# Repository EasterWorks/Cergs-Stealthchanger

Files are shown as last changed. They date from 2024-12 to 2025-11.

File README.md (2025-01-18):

# Cergs-Stealthchanger

Repo status: READY (ready for public reference)  

This repo contains my configurations and customizations for my Stealthchanger build.  

This repo may be useful to you if you have similar design constraints and requirements to my own:

- You have a 300mm Voron 2.4r2.
- Your mainboard is a BTT Octopus Pro or board with similar capabilities.
- You want to use Stealthburner toolheads with the E3D Revo hotend ecosystem.
- You are using LDO's Nitehawk-SB or Nitehawk-36 toolhead boards and Isik Tech's Birds' Nest for toolhead board networking.
- You are using the standard X/Y endstops that are located on the intersection of the X and Y axiis rather than the toolhead-mounted endstops or sensorless homing.
- You are want to use OptoTAP v2.4.1 for your Z axis probe and endstop trigger.
- You are me in the future and nuked your config files again or forgot how to calibrate something.

In addition, I have edited and provided a few STL's that improve upon the original design and/or make it more suitable for the above considerations.  

This repo is under construction. The top line of this readme document says "Repo status" - I will keep this up to date as I update my progress on the toolchanger project.

If you have any questions about necessary plugins or part designs, please reach out to the original creators (whom will be listed and credited when their content is used). I also HIGHLY recommend joining the public Stealthchanger Discord channel, link here: https://discord.gg/kXuEYBsa

## Mile-High Overview of the Stealthchanger

[This](https://github.com/EasterWorks/Cergs-Stealthchanger/blob/main/mile-high-overview-of-the-stealthchanger.md) is a shorter document than the Hardware and Calibration document which is going to cover the basic concepts as a toe-dip. 

## How to Stealthchanger

I have created a guide in this repo that covers all the steps I took from day 1 to fully-functional. You can find it here: https://github.com/EasterWorks/Cergs-Stealthchanger/blob/main/Hardware-And-Calibration.md

## Extrapolation

You will notice that there is a folder named "Extrapolation". This includes experiments I've done with the Stealthchanger ecosystem to try to make it more approachable, more reliable, and overall improved. It primarily has a focus on lessons learned for now, but I will include files and information for anything that I tried that I found particularly valuable as well.

## Credits:  
Viesturz, "tapchanger"  
- https://github.com/viesturz/tapchanger  

DraftShift Design, "StealthChanger"  
- https://github.com/DraftShift/StealthChanger  

DraftShift Design & Viesturz "klipper-toolchanger"  
- https://github.com/viesturz/klipper-toolchanger (use this one until DraftShift greenlights their version for public use!)
- https://github.com/DraftShift/klipper-toolchanger  

Thiessen with DraftShift Design for being INCREDIBLY helpful and patient with helping the community find answers when needed.

The Stealthchanger community for being encouraging and offering guidance.

All the people I've linked under printed part recommendations in the above guide.

## Updates:

12/13/2024:  
- Added my initial configs assortment. Some are incomplete.  

12/24/2024:
- Added OrcaSlicer start gcode.

12/29/2024:
- Updated all CFG files as the project is now functional (in testing)

12/30/2024:
- Final touches on cfg examples.
- Refined and added a ton of info to the guide document.
- Updated repo status from "IN TESTING" to "READY".

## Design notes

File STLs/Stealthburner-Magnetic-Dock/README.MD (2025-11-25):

Current options allow for both Revo and Repido 2 hotends (credit to nicksnoopy on Discord for the Rapido 2 files). Uses 8x 6x3mm Neodymium magnets (recommend N52). Adhere to shaped cutouts using heat-tolerant superglue or epoxy (I find that Loctite Professional Liquid is sufficient for 50-60c chamber temps).

- dock-base.stl:
Replaces the base piece from the Modular Docks repo. Needs 4x magnets.

- [hotend]-front.stl:
SB front hotend assembly for chosen hotend. Needs 2x magnets.

- [hotend]-rear.stl:
SB rear hotend assembly for chosen hotend. Needs 2x magnets.

Rapido V2 files provided by nicksnoopy on Discord.

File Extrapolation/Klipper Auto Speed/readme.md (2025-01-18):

Once your Stealthchanger is functioning reliably, I have found it valuable to run Kilpper Auto Speed by Anonoei, which you can find here:

https://github.com/Anonoei/klipper_auto_speed

For improving clarity, here is the entire process:

### Ensure Klippy-env is up to date:

```
sudo apt install python3
sudo apt install python3-numpy
sudo systemctl stop klipper
python3 -m venv --update ~/klippy-env
~/klippy-env/bin/pip install -r "~/klipper/scripts/klippy-requirements.txt"
```

### Install Klipper Auto Speed:

```
cd ~
git clone https://github.com/Anonoei/klipper_auto_speed.git
cd klipper_auto_speed
./install.sh
```

Note: Make sure you copy and paste the second line including the repo link into your SSH terminal. I initially typed it by hand and it prompted me to enter Github user credentials. If you copy and paste it, however, it doesn't do that. (shrug)

### Update Printer.cfg:

Copy and paste this to the bottom of your printer.cfg file (don't uncomment the commented-out lines):

```
[auto_speed]
#axis: diag_x, diag_y  ; One or multiple of `x`, `y`, `diag_x`, `diag_y`, `z`

#margin: 20            ; How far away from your axes to perform movements

#settling_home: 1      ; Perform settling home before starting Auto Speed
#max_missed: 1.0       ; Maximum full steps that can be missed
#endstop_samples: 3    ; How many endstop samples to take for endstop variance

#accel_min: 1000.0     ; Minimum acceleration test may try
#accel_max: 50000.0    ; Maximum acceleration test may try
#accel_accu: 0.05      ; Keep binary searching until the result is within this percentage

#velocity_min: 50.0    ; Minimum velocity test may try
#velocity_max: 5000.0  ; Maximum velocity test may try
#velocity_accu: 0.05   ; Keep binary searching until the result is within this percentage

#derate: 0.8           ; Derate discovered results by this amount

#validate_margin: Unset      ; Margin for VALIDATE, Defaults to margin
#validate_inner_margin: 20.0 ; Margin for VALIDATE inner pattern
#validate_iterations: 50     ; Perform VALIDATE pattern this many times

#results_dir: ~/printer_data/config ; Destination directory for graphs
```

Note: Technically you only need to include "[auto_speed]", but I advise grabbing the params as well so you can adjust if needed.

### Running Auto Speed:

Klipper Auto Speed has several macros you can utilize, though the fast way to do this is to just use AUTO_SPEED. You can append AXIS=[axis] to specify the axis you want to test. Example:

You want to test the Z axis.
```
AUTO_SPEED AXIS=Z
```

If you DON'T specify an axis, the X and Y axes will be tested.

Of incredible importance: Ensure your X/Y/Z max positions are accurate. My Voron 2.4 on paper has a 300mm max Z position, but in practice, it actually runs into hardware limitations at 280mm. I had never edited this parameter to be accurate to reality, so it was still set to 300mm, and my gantry tried to go to heaven when I first tried to test the Z axis. 

### What it does and how it works:

AUTO_SPEED will take around 5-10 minutes to run for each axis. It will home many times during this process.

For its testing procedure, Auto Speed will home the gantry to measure zero position, then do a short, quick move on the axis/axes being tested. Once done with the quick move, it will re-home and compare the home position to where the tool believed it was after the quick move. This determines step loss.

As the procedure continues, the short, quick moves will become more and more aggressive until Klipper Auto Speed sees a more than acceptable number of steps are being lost. It will then present max speeds and accelerations in the following format over the console:

```
AUTO SPEED found recommended acceleration and velocity after 243.31s
| DIAG X max: a23487 v421
| DIAG Y max: a23487 v421
Recommended accel: 23487
Recommended velocity: 421
```

### What to do with the results:

The results that Klipper Auto Speed will present are essentially the maximum acceptable **travel moves** for your printer. You don't want to run the printer at its absolute max all the time, so take about 20% off the top and use those as your new speed and acceleration maxes for the relevant axes.

After doing this and restarting firmware, I advise running a QGL with your finger on the E-stop. QGL will use the max X/Y/Z speeds and accelerations for travel moves. If you hear groaning, belt skipping, or anything else concerning, dial back the speed by another 10%. Repeat until expensive sounds stop happening, then slowly increase it until they start again. Then decrease slightly below that level, and you have your max X/Y/Z travel movements.

### Use case:

The default speeds and accelerations for the Z axis in the Voron 2.4 printer.cfg are :

```
max_z_velocity: 15 			#Max 15 for 12V TMC Drivers, can increase for 24V
max_z_accel: 350
```

In my experience, even doubling that default speed to 30 since Vorons run on 24v, this results in a 24-second toolchange procedure. It could be worse, but it could also be a whole lot better.

After running Klipper Auto Speed, I found the physical limitations of the Z axis were actually quite a lot higher:

```
AUTO SPEED found recommended acceleration and velocity after 619.64s
| Z max: a65974 v3917
Recommended accel: 65974
Recommended velocity: 3917
```

In practice, these were far too high. But using them to understand that my Z axis had very limited mechanical fluctuation helped me feel that I could safely increase speeds. 

My speed and acceleration for the Z axis are now:

```
max_z_velocity: 150
max_z_accel: 400
```

... which has resulted in toolchanges taking 9 seconds.

On top of just simply making toolchanges faster so prints don't take as long, this also helps reduce the ooze that happens when a tool is travelling from the dock to the print. On 24s toolchanges, my tools can ooze around 3-4mm of material, necessitating the use of a purge tower. At 9s, they barely have any time to ooze, meaning a purge tower is no longer mandatory. So not only cutting down toolchange times and reducing ooze, but also eliminating the purge tower, all contribute greatly to overall print speed and reduce the potential for failed prints.

Stats for nerds using the two-color Panda for reference, which has 151 tool changes:

**24-second toolchanges with a purge tower:**
- Total print time: 3h47m
- Time spent on toolchanges: 1h24s
- Time spent actually printing the Panda: 2h46m36s
- Filament used total: 51.81g
- Filament used on purge tower: 2.97g
- Filament used on actual print: 47.84g
- Total filament cost (for Elegoo PLA+ on both colors): $0.83 USD
- Cost of purge tower filament: $0.06 USD
- Cost of actual print filament: $0.77 USD

**9-second toolchanges with no purge tower:**
- Total print time: 2h54m
- Time spent on toolchanges: 22m39s
- Time spent actually printing the Panda: 2h31m21s
- Filament used total: 47.84g
- Filament used on purge tower: 0g
- Filament used on actual print: 47.84g
- Cost (for Elegoo PLA+ on both colors): $0.76 USD
- Cost of purge tower filament: $0 USD
- Cost of actual print filament: $0.76 USD

**Differences**
- ~23.5% less total print time.
- ~9.5% less total materials cost.
- ~5.7% less material waste on purge tower.

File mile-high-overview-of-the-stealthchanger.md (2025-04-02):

# Mile-High Overview of the Stealthchanger

Want a more consise description of the Stealthchanger and don't want to scroll through a ton of Github pages, YouTube videos that only cover fractions of the overall picture, or my huge Hardware and Calibration document? Start here!

### What is Stealthchanger?
[Stealthchanger](https://github.com/DraftShift/StealthChanger) is a toolchanging system by DraftShift Design based on Viesturs Zariņš' [Tapchanger](https://github.com/viesturz/tapchanger) project. Stealthchanger uses a different shuttle design than the Tapchanger and supports a wide array of toolheads.

DraftShift Design's toolchanger project will _eventually_ be a hollistic overhaul of Tapchanger and Klipper-Toolchanger, but their firmware scripts are still in the prototype stage as of this writing, so they are currently leaning on Viesturs' framework - this will _eventually_ change, but for now, you can't have Stealthchanger without Tapchanger.

### How does Stealthchanger work?
On the hardware side, the original Voron 2.4 toolhead shuttle is replaced with one that has embedded magnets and sleeve bearings. Instead of mounting directly to the shuttle, toolheads now mount to a backplate, which is equipped with a magnet, some screws for adjusting interface angle, and some pins to match the sleeve bushings in the new shuttle.

On the software side, Stealthchanger relies upon an add-on package called [klipper-toolchanger](https://github.com/viesturz/klipper-toolchanger). This includes routines, functions, and macros that are used to dynamically equip different toolheads as they are called from customized gcode in your slicer software.

### What printers is it compatible with?
Stealthchanger and Tapchanger are both configured to work with Voron 2 printers, specifically the [Voron 2.4r2](https://vorondesign.com/voron2.4) (the current iteration of the Voron 2.4 at the time of this writing), but some compatability is present with the design prior to revision 2 which used MGN-9 rails instead of MGN-12 rails. DSD is currently working internally on making a compatible version for the Voron Trident as well.

Ultimately, the shuttle, backplates, dock, and add-ons/scripts may be able to function with any Klipper-based 3D printer, but if you're installing it on any printer than the Voron 2 series, significant adaptation/customization will be required.

### How hard is it to build and set up?
Setting up the Stealthchanger is only going to be difficult in the following scenarios:
- You have difficulty customizing .cfg files due to lack of understanding how Klipper works.
- You aren't familiar with gcode macros and variables.
- Your printer is not calibrated well.

I'd say you only need a basic comprehension of Klipper programming and gcode writing to get things working, as long as your printer is calibrated well and producing good-quality and accurate prints. I have done my best to write my [Hardware and Calibration document](https://github.com/EasterWorks/Cergs-Stealthchanger/blob/main/Hardware-And-Calibration.md) as if the reader didn't know anything about the configuration options and installation/calibration process, and I'm constantly updating it to clarify wording, add little things I didn't consider including initially, and so on.

### What kind of tools do I need to have?
Just the normal stuff!
- A computer with SSH connectivity capabilities.
- Wire cutters.
- Hobby knife.
- Files/sandpaper.
- Wire strippers.
- Crimping tool.
- Soldering iron, ideally with an M3 heat-set insert tip.
- Zipties
- Pliers.

Basically just the normal tools you'd need for maintaining a 3D printer.

### What print settings should I use?
DSD recommends printing Stealthchanger components to Voron specifications. These are as follows:
- Layer height: 0.2mm
- Extrusion width: 0.4mm (forced)
- Infill density: 40%
- Infill type: Grid, gyroid, honeycomb, triangle, or cubic
- Wall count: 4
- Top/bottom layers: 5

The one exception is that you WILL need to use supports for the Stealthchanger shuttle, but backplates and most of the dock parts are designed to print unsupported.

### Is there a guide on how to do this project from start to finish?

I have written a [Hardware and Calibration](https://github.com/EasterWorks/Cergs-Stealthchanger/blob/main/Hardware-And-Calibration.md) document that covers everything from bill of materials and print selection to installation, calibration, and customized slicer gcode settings. It is fairly comprehensive, but still a work-in-progress. It should have enough information to at least fill in gaps and help figure out what you need to research further.

Otherwise, DSD has a Discord channel specifically for the Stealthchanger project, and there are a lot of helpful folks there willing to help where you get stuck. Be polite and respectful. Invite link: https://discord.gg/kXuEYBsa

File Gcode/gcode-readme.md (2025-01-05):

## THE SUPPLIED MACHINE_START AND MACHINE_END GCODE ARE TAILORED FOR ORCASLICER. Not guaranteed to work in Bambu Studio. Will not work in SuperSlicer forks.

## Both the Start and End gcodes reference my renamed "TOOLCHANGER_PRINT_START" and "TOOLCHANGER_PRINT_END" macros from toolchanger_macros.cfg.

# Machine Start
Enter this in the Machine Start field in OrcaSlicer under Machine Settings in the Machine Gcode tab. This gcode is identical to the start gcode provided in the Stealthchanger and Tapchanger repos, simply has the PRINT_START macro renamed.

# Change Filament Gcode
Enter this into the Change Filament Gcode field in OrcaSlicer under Machine Settings in the Machine Gcode tab. 

I was running into a problem where in the following two instances:
- Multiple toolheads would be working on the first layer
- A toolhead other than T0 was being used for the first layer after T0 completed the bed mesh

... that any tool other than T0 would not heat after being picked up, causing Klipper to throw an "extrude below minimum temp" error and cancel the print as part of its thermal runaway protection. 

The Change Filament Gcode I have provided handles this by throwing the first layer temperature value from the filament settings at the next toolhead explicitly on every change. This is a bit of a WIP because it's only piping through the first layer temp (not the "other layers temp"), but I'm working on a fix for that. For now - it's totally usable, but suboptimal.

# Machine End
Enter this in the Machine End field in OrcaSlicer under Machine Settings in the Machine Gcode tab. This is identical to the end gcode provided in the Stealthchanger and Tapchanger repos, simply has the PRINT_START macro renamed.

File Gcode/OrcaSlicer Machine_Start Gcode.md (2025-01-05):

# Start Gcode for OrcaSlicer
This is the gcode from the Toolchanger github repo, but I have changed "PRINT_START" to "TOOLCHANGER_PRINT_START" to match the edits made in my toolchanger.cfg file in this repo. This will accomodate for up to 6 toolheads. If you are planning on adding more than 6, you will need to iterate more of these "{if is_extruder_used[#]}T#_TEMP={first_layer_temperature[#]}{endif} " lines. This all needs to be copy and pasted as one line into your Start Gcode field in Orca Slicer. You can omit these comment lines.

```
;machine_start
TOOLCHANGER_PRINT_START TOOL_TEMP={first_layer_temperature[initial_tool]} {if is_extruder_used[0]}T0_TEMP={first_layer_temperature[0]}{endif} {if is_extruder_used[1]}T1_TEMP={first_layer_temperature[1]}{endif} {if is_extruder_used[2]}T2_TEMP={first_layer_temperature[2]}{endif} {if is_extruder_used[3]}T3_TEMP={first_layer_temperature[3]}{endif} {if is_extruder_used[4]}T4_TEMP={first_layer_temperature[4]}{endif} {if is_extruder_used[5]}T5_TEMP={first_layer_temperature[5]}{endif}  BED_TEMP=[first_layer_bed_temperature] TOOL=[initial_tool]
```

# Change Filament Gcode for OrcaSlicer
I have also found that some specific Change Filament G-code is needed (a few fields beneath the machine_start gcode text field) if you want to be able to print two or more materials on the same first layer. This is what I use:

```
;change filament gcode
M104 S{first_layer_temperature[next_extruder]} T[next_extruder]
T[next_extruder]
M109 S{first_layer_temperature[next_extruder]} T[next_extruder]
```

This forces Klipper to send the command to get the next tool up to heat before the toolchange, and to wait for the tool to get up to temp before picking it up. After the first layer, the preheating gcode commands from the slicer will kick in (you configured those, right???) - these commands will still go through, but they'll get processed quickly since the next tool should already be hot at this point. **NOTE THAT** this gcode is calling "first_layer_temperature[next_extruder]". This means it's grabbing the first layer temp from your filament settings, not the "other layers" temperature. I'm working to find a workaround for this that will use logic statements to decide if the next tool is working on layer 1 or any layer beyond that, and apply the correct temperature if possible. I will update this document once I've figured that out :-)

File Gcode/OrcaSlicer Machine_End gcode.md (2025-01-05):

We don't do anything fancy for this, just pipe through the TOOLCHANGER_END_PRINT gcode macro. Copy and paste the below into your end gcode field in Orca Slicer:

```
;end print gcode
TOOLCHANGER_PRINT_END
```

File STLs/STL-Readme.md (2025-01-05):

# Explanation of STL files in this folder

### shuttle_redesign.stl:
This is a replacement for the shuttle in the Stealthchanger repo that adds channels for excess belt pathing. The intention is that you will thread your belts around the "corner" and into the available channels as far as possible, then trim anything that sticks out of the sides. This both helps install the shuttle without juggling the belts and using strange methods to hold the belts in place and allows for the advisable retention of extra belt length just in case. The two holes for M3 heat set inserts on the bottom have had their positions changed so they don't print as squished as the originals. Actual amount of Y axis travel loss is around 4-5mm depending on your setup.

### zero_clearance_supports.stl
This is an **OPTIONAL** part for printing the shuttle with a pre-made zero-clearance support structure. It SHOULD work with the original DSD shuttle design, but I haven't tested it with that yet. This is intended for you to use _after_ you already have your Stealthchanger assembled in the event you'd like to use a higher quality material, or simply to get a """"better""" shuttle print, but you could feasibly do it with manual filament changes if you're okay with sitting there watching for 64 tool changes. 

Print settings:
- Import this into OrcaSlicer, set it to be printed with your tool that is loaded with PLA, PLA+, or PLA Repid. Set its position to the center of the bed.
- Import MGN12-shuttle.stl and set that to print with your main printing material. Center its position on the build plate so it sits squarely on top of the support structure. Use the sensor probe tab at the "top" of the shuttle to assist with alignment on x/y if needed.
- First layer should be 0.25mm.
- Use the normal 4 walls, 5 tops/bottoms, and 40% infill recommended for the project.
- For the support structure, ensure all top surfaces are ironed.
- Increase your PLA build plate temperature to match the build plate temperature of the material you're using for the shuttle.
- **NOTE**: This is **NOT NECESSARY** for a functioning shuttle! Some people can't resist the urge to print it with a super clean rear face, and some people might want to sell printed parts kits that look visually stunning all around - this will do it. 

### x-axis-prod.stl
Both the default shuttle and my above redesign won't have sufficient width to hit the X axis limit switch without crashing into the gantry. This is a small plate that screws into the bottom of the above shuttle with two M3x8 SHCS screws and sticks out just enough to hit the trigger before the gantry crashes. NOT compatible with the DSD shuttle design due to different hole placement intended for better printing.

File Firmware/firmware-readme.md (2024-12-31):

# Description of CFG files:

As a forenote here: most people leave the folder for all of the Toolchanger and Stealthchanger-specific cfg's in a folder called "Tapchanger" because that's how the original configs are built. I have changed this folder to be named "Stealthchanger" as that's more fitting. This is a personal choice, do what you prefer but pay attention if you name it something other than "Stealthchanger"!

### printer.cfg
Naturally, this is your printer's config file. It's where the baseline definitions for where hardware is connected to on your mainboard lives. Note that things like the probe section and extruder config have been removed - those are now in t0 and t1 CFG's. Also note the includes and their order. This is a modification of the default Voron V2.4r2 printer.cfg example from Klipper.

### toolchanger.cfg
This is where almost everything Toolchanger-specific is going to live. All you really need to change here are "params_safe_y" and "params_close_y". More info on that in "Docking Calibration" in the calibration manual linked below. This is from the Klipper-Toolchanger repo.

### toolchanger_macros.cfg
This is where the Toolchanger-specific macros go. Note that I have changed the PRINT_START and PRINT_END macro names to "TOOLCHANGER_PRINT_START" and "TOOLCHANGER_PRINT_END", and commented out a few lines that only seemingly exist to report errors. I may uncomment those eventually but when I see "unknown command" in the terminal and the command doesn't appear to do anything, it will get excluded. This is from the Klipper-Toolchanger repo.

### stealthchanger_macros.cfg
This includes some additional and entirely optional macros. You don't have to use this. This is from LDO's documentation.

### t#.cfg
This is the cfg for your toolhead! I have added a few notes to the CFG's provided in this repo where you need to pay extra attention. This is a combination of the tool examples in the Tapchanger repo and from LDO's documentation.

### tool_detection.cfg
This cfg includes the crash detection functionality and is important for avoiding accidents. I'm not super sure why it's seprate from the main toolchanger.cfg file, but as presented it shall stay on my printer. This is from the klipper-toolchanger repo.

### calibrate_offsets.cfg
This cfg includes some functionality for calibrating the nozzle offsets between different toolheads using probes like Sexball. I do adjustments with a test print and a digital depth gauge, which I cover under "Nozzle Offsets - probe-to-nozzle and gcode" in the calibration manual linked below. This is from the klipper-toolchanger repo.

### homing.cfg
This cfg includes the new homing override you'll want to use, sensorless homing functionality (which I have commented out because we're using physical endstops here), and some tool offset functionality for homing, gcode, and meshing. The latter three aren't called in my config but are there for testing if needed. This is from the klipper-toolchanger repo.

# Calibration manual:
https://github.com/EasterWorks/Cergs-Stealthchanger/blob/main/Hardware-And-Calibration.md

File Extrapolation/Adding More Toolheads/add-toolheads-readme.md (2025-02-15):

After completing the initial build with the two Stealthburner toolheads, I wanted to add two more toolheads - in particular, Dragonburners with the WWBMG extruder and the LDO Nitehawk-36 toolhead board.

Assembly of the tools and dock parking calibration is as straightforward as it is for building any other set. However, something to note is that the nozzle on the bottom of the Stealthburners protrudes downward FAR more than the nozzle on the Dragonburners, meaning extra care must be taken when calibrating the Dragonburner's Z offset.

Additionally, I was not able to get the Dragonburner cowl and dock bases provided by DraftShift Design working properly. The core issue was that the Dragonburners are VERY likely to tilt on the two screws that grab into the cowl when being picked up by the shuttle, making docking/undocking incredibly inconsistent.

To get around this, I designed a new cowl and dock which rely upon 5x2.75mm magnets, which can be found in this same folder under "Dragonburner-Magnets". This bulks out the fan duct sections of the cowl slightly to add real estate for four magnets, and modifies how the toolhead sits in the dock base and also provides space for four matching magnets. An additional two 5mm magnets can be placed in front of the cowl screws to mate up to some M3 machine screws for added stability and guidance during docking/undocking.

### big huge important note
You will likely have times where you want to comment out one toolhead or the other for troubleshooting. I have discovered that, perhaps due to Klipper's internal processing of toolhead numbers, you can't non-consecutively comment out toolheads from your printer.cfg without running into problems. For example: You have four tools, t0-t3. You comment out the include for t2 as you're trying to narrow down an issue that doesn't affect that toolhead, but you leave t3's include uncommented. Upon rebooting klipper, you will get errors about pin assignments for extruder3 / t3 being invalid. In order to successfully comment out t2, you will also have to comment out t3, otherwise you will get errors such as this. Kind of a ballache if you need to troubleshoot a non-sequential tool, but you can also just switch around MCU ID's temporarily if you have to.

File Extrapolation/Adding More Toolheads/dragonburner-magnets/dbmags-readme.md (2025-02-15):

Print one "cowl-magnets.stl" and one "dock-base-magnets.stl" per Dragonburner in use. Each toolhead and dock combo will require 8-10 5x2.75mm N52 neodymium magnets.

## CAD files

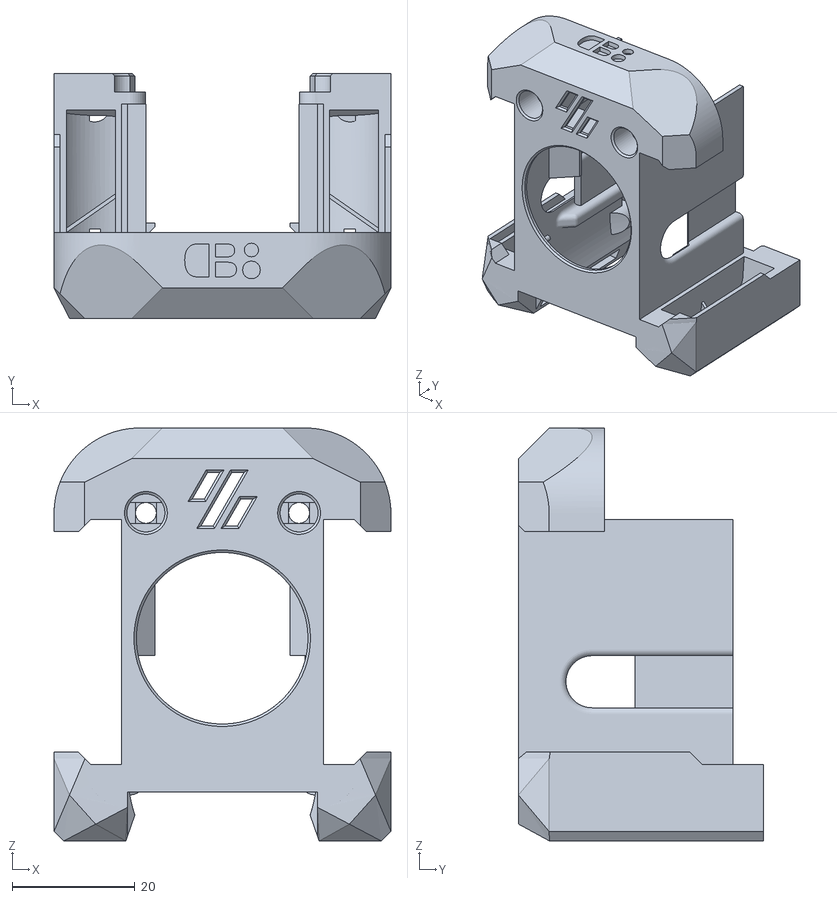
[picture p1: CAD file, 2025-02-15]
Extrapolation/Adding More Toolheads/dragonburner-magnets/cowl-magnets.stl
55.0 x 40.0 x 67.4

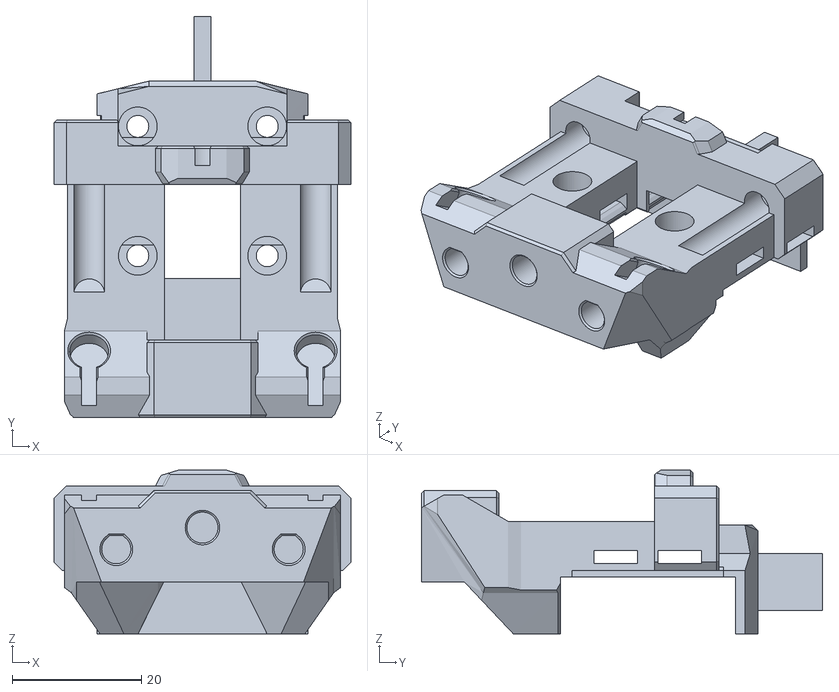
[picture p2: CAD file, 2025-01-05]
STLs/shuttle-redesign.stl
45.9 x 62.0 x 25.3

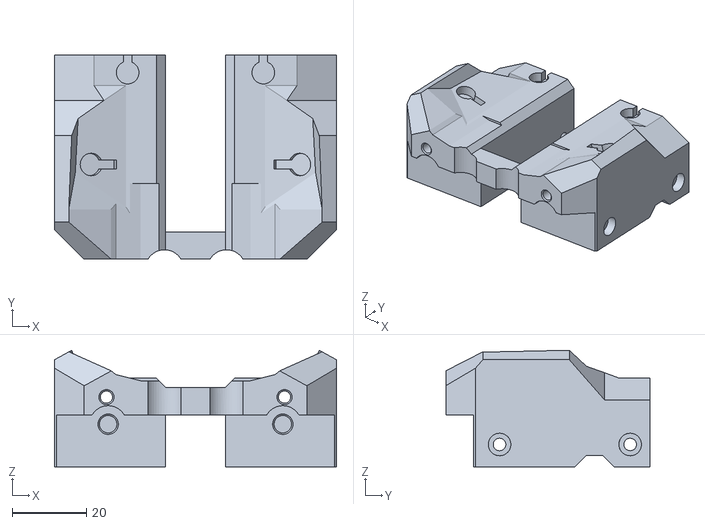
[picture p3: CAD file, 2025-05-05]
STLs/Stealthburner-Magnetic-Dock/dock-base.stl
76.0 x 55.1 x 31.4

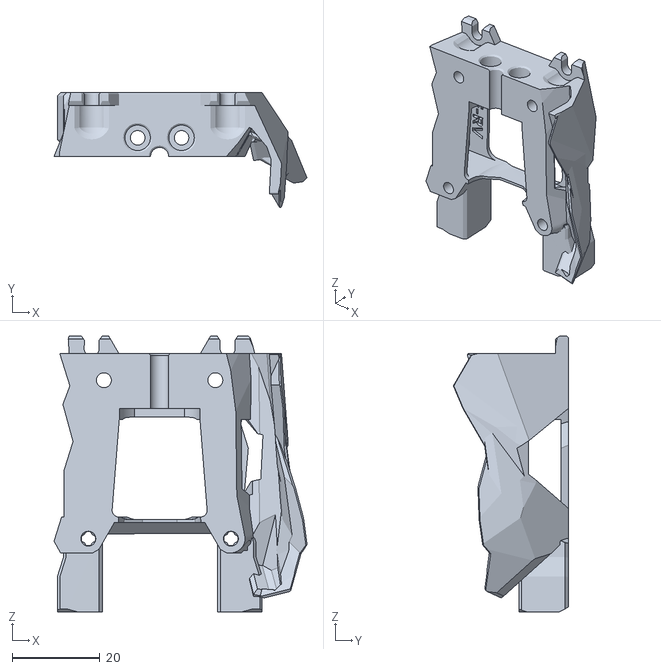
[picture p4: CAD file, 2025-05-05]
STLs/Stealthburner-Magnetic-Dock/E3D Revo/sb-rear.stl
57.7 x 26.3 x 62.9

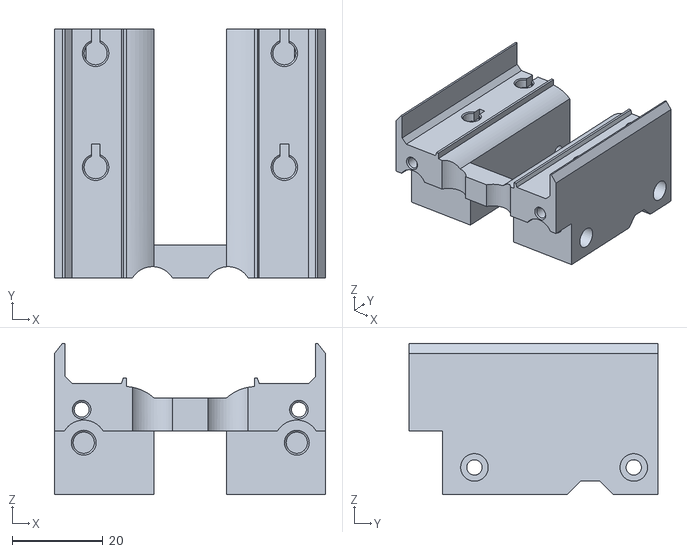
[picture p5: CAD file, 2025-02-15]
Extrapolation/Adding More Toolheads/dragonburner-magnets/dock-base-magnets.stl
59.9 x 55.1 x 33.4

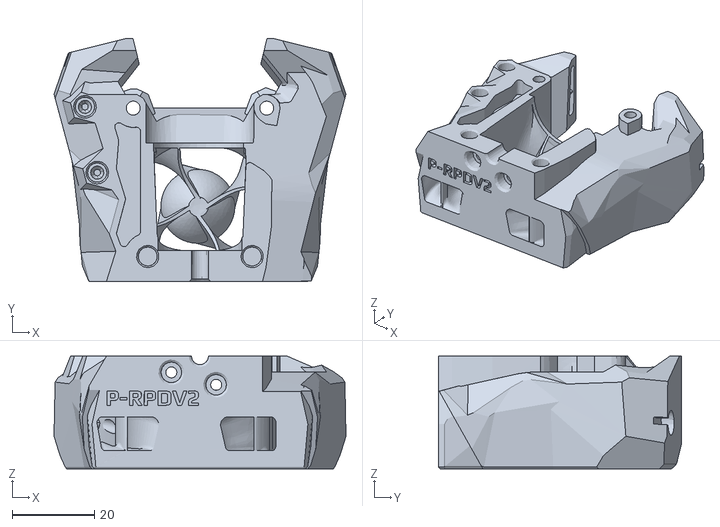
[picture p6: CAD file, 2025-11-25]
STLs/Stealthburner-Magnetic-Dock/Rapido 2/Rapido_v2-front.stl
71.1 x 59.2 x 27.4

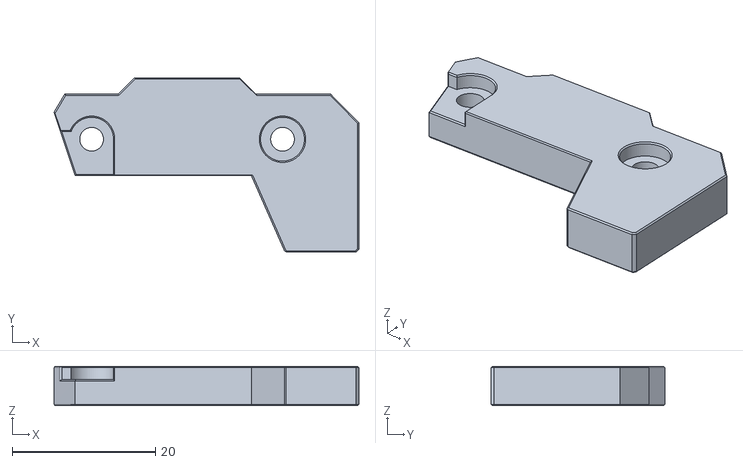
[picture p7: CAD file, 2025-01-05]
STLs/x-axis-prod.stl
42.5 x 24.3 x 5.50

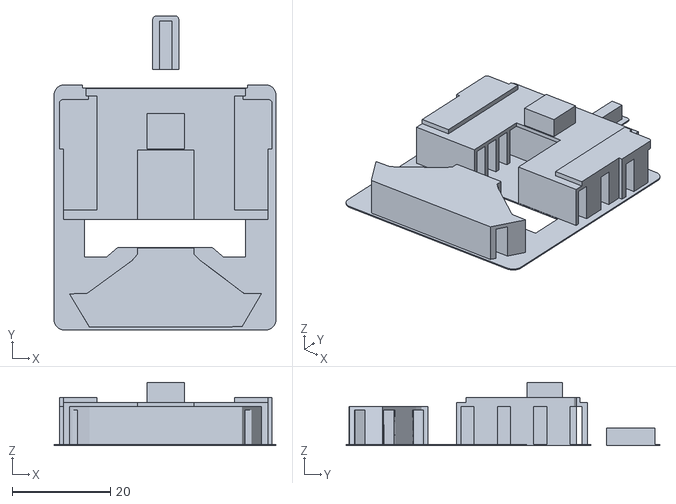
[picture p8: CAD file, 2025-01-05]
STLs/zero-clear_supports.stl
45.2 x 63.9 x 12.9

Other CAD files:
STLs/Stealthburner-Magnetic-Dock/Rapido 2/Rapido_v2-rear.stl

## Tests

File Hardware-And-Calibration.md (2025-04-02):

This page is a WIP kinda but should be full of hopefully helpful information.

# First: USE CAUTION!



### I am not responsible for any silly little mistakes you make during the following process. You need to read this document, think about the parts you don't understand, and do research before starting this project. Hot robots can poke you, prod you, burn you, cut you, scrape you, break their own parts, break YOUR own parts, electocute you, and even burn your house down if you aren't careful. Tinker responsibly!

# HOW DO I STEALTHCHANGER?
Complete the following sections in order to replicate my process.

# Table of Contents
- [Add-Ons and Updates for Klipper](https://github.com/EasterWorks/Cergs-Stealthchanger/blob/main/Hardware-And-Calibration.md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)
- [Bill of Materials](https://github.com/EasterWorks/Cergs-Stealthchanger/blob/main/Hardware-And-Calibration.md#bill-of-materials)
- [Printed Part Selection](https://github.com/EasterWorks/Cergs-Stealthchanger/blob/main/Hardware-And-Calibration.md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)
- [Preparing, Assembling, and Installing the Shuttle](https://github.com/EasterWorks/Cergs-Stealthchanger/blob/main/Hardware-And-Calibration.md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)
- [Preparing, Assembling, and Installing the Backplates](https://github.com/EasterWorks/Cergs-Stealthchanger/blob/main/Hardware-And-Calibration.md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)
- [Preparing, Assembling, and Installing the Tophat (not in the BOM!)](https://github.com/EasterWorks/Cergs-Stealthchanger/blob/main/Hardware-And-Calibration.md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)
- [The Dock Crossbar and Bulking Out the Front of the Printer (not in the BOM!)](https://github.com/EasterWorks/Cergs-Stealthchanger/blob/main/Hardware-And-Calibration.md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)
- [Heat-Treating Process for Backplates](https://github.com/EasterWorks/Cergs-Stealthchanger/blob/main/Hardware-And-Calibration.md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)
- [Other Assembly Notes](https://github.com/EasterWorks/Cergs-Stealthchanger/blob/main/Hardware-And-Calibration.md#other-assembly-notes)
- [Special Notes on OptoTAP](https://github.com/EasterWorks/Cergs-Stealthchanger/blob/main/Hardware-And-Calibration.md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)
- [Running Your Umbilical Cables](https://github.com/EasterWorks/Cergs-Stealthchanger/blob/main/Hardware-And-Calibration.md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)
- [Nozzle Offsets - Probe-to-Nozzle and Gcode](https://github.com/EasterWorks/Cergs-Stealthchanger/blob/main/Hardware-And-Calibration.md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) 
- [PID, Input Shaper, Extruder Rotation Distance, and Pressure Advance Tuning](https://github.com/EasterWorks/Cergs-Stealthchanger/blob/main/Hardware-And-Calibration.md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)
- [Dock Parking Calibration, Testing, and Safe Zone Specification](https://github.com/EasterWorks/Cergs-Stealthchanger/blob/main/Hardware-And-Calibration.md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)
- [Purge, Preheat, and Other Relevant OrcaSlicer Settings](https://github.com/EasterWorks/Cergs-Stealthchanger/blob/main/Hardware-And-Calibration.md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) 
- [Machine Start, Change Filament and Machine End Gcode](https://github.com/EasterWorks/Cergs-Stealthchanger/blob/main/Hardware-And-Calibration.md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) 
- [Nozzle Offsets - X/Y Offset](https://github.com/EasterWorks/Cergs-Stealthchanger/blob/main/Hardware-And-Calibration.md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) 
- [Musing on silly things I didn't think about at first](https://github.com/EasterWorks/Cergs-Stealthchanger/blob/main/Hardware-And-Calibration.md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) 
- [Final Considerations](https://github.com/EasterWorks/Cergs-Stealthchanger/blob/main/Hardware-And-Calibration.md#final-considerations) 

# Add-Ons and Updates for Klipper

**First: BACK UP YOUR CURRENT CFG'S!!!!!**

You will need to install the following Klipper add-ons:
- Klipper-Toolchanger: https://github.com/viesturz/klipper-toolchanger/

This includes everything Klipper will need for the actual toolchanging routines, running multiple part fans, managing multiple probes, incorporates some path rounding logic for non-print moves (docking/undocking, ect) and some calibration utilities. You will need to edit some of these files: Check in the "Firmware" folder in this repo for comments pointing out where.

Make sure Klipper is up-to-date before beginning, and if necessary, update Klipper on your Bird's Nest and your Nitehawk toolhead boards. Proper functionality apparently relies upon features updated/added to Klipper around July of 2024, so you need a version that's newer than that. When you buy the Bird's Nest from Isik and the Nitehawks from LDO, they _should_ already be on the latest release of Klipper when you receive them, but it's good to double-check.

Once you have finished updating Klipper and installing the klipper-toolchange add-on package, grab the config files I have posted in the Firmware folder under klipper-examples and add all of them to a new folder under your Klipper directory called "Stealthchanger", with the exception of printer.cfg. Go through both my and your printer.cfg files and transpose over everything that's different to yours - then go through the T0 and T1 configs to ensure they are correct for your toolheads and make the needed adjustments. After that, go through the remaining config files and look for any notes I've left - I have left comments areas of exceptional importance to ensuring this works as well as it possibly can for you as a starting point.

# Bill of Materials

Remember that this repo is centered around the concept of implementing the Stealthchanger with two Stealthburner+Revo toolheads using LDO Nitehawk-SB toolhead boards and an Isiks Tech Birds' Nest for toolhead networking. If you are using CAN or different toolhead designs, this won't be entirely accurate.

### Stealthburner:
- [LDO Nitehawk-SB](https://west3d.com/products/nitehawk-stealthburner-toolboard-sb-pcb-by-ldo-motors) (one per toolhead) 
- [E3D Revo hotend](https://www.filastruder.com/products/e3d-revo-voron?variant=39567818981447) (one per toolhead)
- [4mm ECAS fitting](https://www.amazon.com/Pneumatic-Connector-Fittings-Extruder-Accessories/dp/B0CB6SJBS9) (one per toolhead)
- All other commercial parts needed for the Stealthburner can be found [here](https://vorondesign.com/voron_stealthburner), with the exception of the Cables and Optional - ADXL345 Sensor sections.

The main difference between the standard Stealthburner and the Stealthchanger adaptation is that instead of putting heat sets and screws into the original Voron 2.4 shuttle, you'll instead be putting those parts into the backplates.

### Shuttle
- 6x3mm N52 neodymium magnet (x3)
- 4x6x6mm oilless sleeve bushing (x3)
- M3x8 SHCS (x4)
- M3x5x4mm heat-set inserts (x2)

### Backplate (each):
- OptoTAP optical sensor (x1)
- 6x3mm N52 neodymium magnet (x1)
- M3x6 FHCS (x2)
- M3x6 BHCS (x2, used to retain the OptoTAPs - may also use M3x8, just screw them in slowly)
- M3x8 SHCS (2x)
- M4x12mm round-head dowel pins (x3)
- M3x5x4mm heat-set inserts (4x)

### Dock (each):
- M5x8 BHCS (2x)
- M5 T-nut/hammer nut (2x)
- M3x8 SHCS (x2)
- M3x8 BHCS (x4)
- M3x30 SHCS (4x)
- M3x60 SHCS (x2)
- M3 heat-set inserts (x10)

If you would like to print any of the wiper options, ensure you instead print the "Stubby" spring steel body and pay attention to the changes therein.

# Printed Part Selection

As this repo is targeted toward people wanting to use the Stealthburner toolhead, we'll first talk about that.

### ECAS fitting for Clockwork 2


First up: I HIGHLY advise printing a CW2 housing with allowance for an ECAS fitting. I used this one by AlexanderT_Moss on Printables:
- https://www.printables.com/model/433797-clockwork-2-ecas-fitting-for-ercf

The reason for using an ECAS fitting is because the reverse bowden tubes will be flexing around a bit more than usual when constrained to the umbilical, so it will benefit from stronger retention. Make sure to print the modified latch as well since it needs to be able to clear the ECAS fitting.

### Backplates and Shuttles


Next you'll need both the Stealthburner backplates and a shuttle. Here are the backplates from the DraftShift Design repo:
- https://github.com/DraftShift/StealthChanger/blob/main/STLs/Backplates/StealthBurner.stl

As for the shuttle, I have modified DSD's design to allow you to loop the belts back into and out of the housing to prevent cutting the belts too short. It can be found in this repo:
- https://github.com/EasterWorks/Cergs-Stealthchanger/blob/main/STLs/MGN12%20Shuttle.stl

Of course you may also use the DSD version of the shuttle without those channels to minimize Y axis travel loss, though routing the belts will be more difficult **and my X axis endstop prod will NOT work with their design**:
- https://github.com/DraftShift/StealthChanger/blob/main/STLs/Shuttle%20MGN12%20(With%20belt%20grooves).stl

DSD also provides a version of the shuttle without the grooves if you prefer that.

YOU WILL NOTICE the "fin" on top of my shuttle redesign is too long for the backplate to sit properly with both parts straight off of the printer. Leave it this way until the shuttle is installed and you have a backplate outfitted with pins. CAREFULLY trim the fin on top of the shuttle until whichever backplate is going on your T0 sits as flat to the shuttle as it's going to (force it if needed - poor fitup will be adjusted later). I found the default height of the fin to be too short.

It is also worth noting that this will move your Y axis about 5mm toward the "front" of the printer. You may need to adjust how your bed is positioned to accomodate.

You also need one backplate per toolhead and only one shuttle. Those can be found on DSD's repo. The link below is for the Stealthburner, but they support many toolheads and the list is growing:
- https://github.com/DraftShift/StealthChanger/blob/main/STLs/Backplates/StealthBurner.stl

Additionally, since we're going to use the X axis endstop on the X/Y intersection joint, you will need to print the X axis prod included in this repo:
- https://github.com/EasterWorks/Cergs-Stealthchanger/blob/main/STLs/x-axis-prod.stl

The X axis prod is secured to the bottom of the shuttle using two M3x8 SHCS that screw into two M3 hot-sets you'll need to embed into either shuttle design in the provided holes. Its job is to touch the X axis endstop when it reaches its maximum travel. DSD has provided endstop triggers which serve a similar purpose to their design and can be found in their repo - I didn't realize this initially, hence designing my own, but I do also prefer the design I came up with, so I'm leaving it here. Use whichever one works best for you.

If you DO NOT want to use my designs and prefer to use DSD's, you can get similar behavior from their shuttle design by printing their belt keeper:
- https://github.com/DraftShift/StealthChanger/blob/main/STLs/Extras/Shuttle_Keeper_6mm_MGN12H.stl

You will also need their shuttle and X-axis prod, naturally.

### PG7 gland mount for Stealthburner


Last part for the toolhead itself - you'll want a PG7 gland mount on the Stealthburners to replace the original X axis dragchain mount. I use this one by CstmCreations_174350 on Printables:
- https://www.printables.com/model/463220-voron-cw2-stealthburner-ebb-sb2240-pg7-umbilical-m

### Umbilical clips


Next up, your umbilical clips. These are largely up to you - I designed ones that would slip over the Nitehawk USB cable, allow a channel for the reverse bowden tube, and use two small zipties to create just enough tension to grip on to the cable and bowden without crushing them. It also has holes to allow for 1mm piano wire as the stiffening component of the umbilical. You can find them here:
- https://www.printables.com/model/1127631-ldo-nitehawk-umbilical-clips-for-stealthchanger-ta

I use four per umbilical.

### Bird's Nest fannypack


Now let's look at making a home for the Bird's Nest and a new exhaust plate to allow the umbilicals into the print chamber. For housing the Bird's Nest, print the fanny pack by Isiks Tech (or another enclosure if you prefer - the fanny pack isn't very space efficient):
- https://github.com/xbst/Birds-Nest/tree/master/Mounts/V2

I used 3M double-sided tape to stick it to the back panel a few inches under the exhaust plate.

### Exhaust Plate / Umbilical Guide


Now for the exhaust plate itself - I designed one that would allow you to non-destrucitvely insert and retain the umbilicals. You can find it here on Printables:
- https://www.printables.com/model/1127639-ldo-nitehawk-umbilical-exhaust-plate-for-voron-24

### Docks
Finally, we need to print our docks. I used low-profile docks that secure to a crossbeam rather than to the top of the printer's frame using parts from three sourcess. The first source, cjackson234 on Printables, provides "base minimal.stl":
- https://www.printables.com/model/994635-stealthchanger-stealthburner-minimal-docks-aka-hap

The second source, arthur belanger on Printables, replaces the multi-part front of the dock with a single-part iteration:
- https://www.printables.com/model/1063297-one-piece-docks-remix-of-crabby-docks/files

The third source is back with DraftShift for their modular docks, particularly the blocker. I used the spring steel body approach to use hobby blades with a molded silicone pad; if you prefer to use the cup style, you can go with that as well:
- https://github.com/DraftShift/ModularDock/tree/main/STLs/Blockers

Finally, back in DSD's repo, you'll need a Stealthburner dock backplate:
- https://github.com/DraftShift/ModularDock/blob/main/STLs/Stealthburner/Back.stl

# Preparing, Assembling, and Installing the Shuttle
All Stealthchanger shuttle designs need to have bushings installed in the corresponding hex-slot holes. Some people glue them in, but the intention is for them to be a near-pressfit. You can find details on the specific bushings in the Bill of Materials section above.

There is a hole for an M3 heat set insert that can go into the bottom center of the shuttle along where the MGN rail shuttle connects - this hole is meant as a securing point for DSD's endstop trigger design. If you're using my shuttle and X-axis prod, you don't need to put a heat set there.

Below the above-mentioned hole, there are two more holes for M3 heat set inserts. Those are to connect the X axis endstop prod in my design, but are absent in the original design. To use the prod, you will also need to print my redesigned shuttle, then secure it to the shuttle with two M3x8 SHCS.

Next, you need 3 6x2mm neodymium magnets. The ones you want to get are N52 with a working temperature rating of 80c. N52 magnets are very strong variants of neodymium and 80c will put you far and beyond the temperature your magnets should ever hit. If you just buy a generic unlabelled pack of neodymium magnets, you will probably get N42s - not as strong, and usually max working temp rating of 60c. These can still work, but I like the strength and safety margins of the N52's, and it's worth a few more dollars for a lifetime supply.

In my redesign of the shuttle, I extended the "fin" at the top so you can trim it only as low as is needed for the backplate to seat fully using some flush cutters. I suggest taking off 1mm of material from that fin at a time until you get the backplate almost fully seated to the shuttle, then file or sand down the rest until your backplate is fully there. The original design has this fin already designed to match up "perfectly" with the backplates - however, in my experience, stacking tolerances lead to that fin sometimes being just slightly too short. 

Finally, you'll notice that the bottom side of the shuttle where the grooves for the 6mm 2GT X/Y axis belts probably printed really ugly. That's fine, realistically all we need here is some surface disruption to grip into the belts. In the STLs folder of this repo, I have added a zero-clearance support structure with some instructions you may use if you wish, but I don't recommend it - this isn't necessary and is only really useful to you if you already have a functional Stealthchanger or other filament-changing printer. On my redesign of the shuttle, just around the corner from those grooves, I have added some channels that you can use to slip excess length of the X/Y belts into - this helps get your belts tensioned properly by giving you somewhere to tug on them while preventing you from cutting your belts too short in case something goes wrong and you need to switch back to your original setup temporarily in an emergency. You DO lose about 4-5mm of Y axis travel because of the needed additional thickness and may therefore need to shift your bed forward that much if you use a nozzle cleaning brush in the rear corner, so be aware of that. If you don't care about having this in a compact one-piece package, there are also belt tensioning guides in the Stealthchanger repo, but I find using additional tools for what should be a fairly simple install to be a bit too much.

To install the shuttle:
- You'll first of course need to fully disengage the X/Y idlers on your gantry to give us some available room for tensioning once the new shuttle is installed.
- Remove the shuttle from your original toolhead. You should be stripping off everything so that your mounting surface is the four tips of the X/Y belts and the MGN12 shuttle.
- Insert the belts into the shuttle in the correct orientation and wrap them back around and into the previously-mentioned channels.
- Insert the 4x M3x8 SHCS screws used to mount the Stealthchanger shuttle on the MGN12 shuttle, but don't tighten them fully - you want to still be able to pull the belts through.
- Pull on both sets of belts with roughly equal tension (the more accurate you are here, the easier tensioning will be). 
- Once you are happy with the tension on the belts, screw the Stealthchanger shuttle down securely to the MGN12 shuttle.
- Returning to the X/Y idlers, apply proper and equal tension to each belt at the X/Y tensioners. Use your favorite trick for tensioning Voron 2.4 X/Y belts, just primarily make sure that it's even and you aren't over-tightening them. This can always be fine-tuned down the line.

# Preparing, Assembling, and Installing the Backplates
Each backplate will require one N52 6x2mm magnet, two M3x6 FHCS, two M3x8 SHCS, four M3 heat-set inserts, and three dowel pins as mentioned in the Bill of Materials section above. Once you install the parts to the backplate and have installed your shuttle on the X axis, skip down to the next section (Heat-Treating Process for Backplates), then return here.

After assembly and heat-treating, attach the backplate to the rear of the Stealthburner using the same screws that were previously used to secure it to the default Voron 2.4 shuttle design. Install the OptoTAP in its position on the rear of the backplate and verify fitup with the shuttle is still solid and snappy. If you notice your backplates are slightly tilted along the X axis, you can back out the two FHCS screws in the backplate to force its alignment with the shuttle, or re-do the heat treating process until the fitup is better. This isn't super commonly needed, but if your backplates didn't come out perfectly, you may experience slight tilting once the entire Stealthburner toolhead is loaded on the shuttle. Some advocate using a "paper test" to check screw alignment - get both screws roughly in the position you'd like and then try to shove a strip of generic A4 printer paper in between the magnet and screw. If both screws are adjusted equally, the paper shouldn't slide under either of them.

# Preparing, Assembling, and Installing the Tophat (not in the BOM!)

In addition to the shuttle, backplates, fanny pack, and docks, you'll need a tophat if you intend to print ABS/ASA and other high temp materials.

There are several options for this. Probably the easiest option is going to be printing the tophat from DraftShift Design:
- https://github.com/DraftShift/Tophat

For my tophat, I simply cut some extrusions to the same dimensions as the top loop of 2020 extrusions on my frame, added vertical struts to make it stand about 8" taller than the top of the frame, assembled them with internal corner brackets, printed some of the default Voron panel clips, and purchased some correctly-sized acrylic panels to cover the tophat frame. Then I mounted it internally to the printer's frame with some printed parallel 2020 mounting plates, which you can find many options for online.

There are many other tophat designs out there as well, including ones with printed frames and acrylic panels if you prefer see-through panels but don't want to deal with the 2020 extrusions. Do some research; ultimately it's up to you. Some people even use a cardboard box. Some _crazy_ people.
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

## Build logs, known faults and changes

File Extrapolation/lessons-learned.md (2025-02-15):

# Lessons Learned

This is going to be a compilation of trials I've done with the Stealthchanger system, particularly in expansion efforts over the original designs.

## Redesigning Parts

I didn't like the idea of cutting my belts exactly to length for the shuttle, so I designed a version of the shuttle which has integrated pathing for looping the belt around, so around 3-4cm of extra belth length can be retained. I found that this was resolved by a part from the SC repo called the shuttle keeper. This does basically the exact same thing, though it's a separate part instead of being integrated directly to the shuttle, so I do still personally prefer my design.

In addition, I designed an X axis endstop trigger as a separate part for the shuttle. The SC repo does have an option for this as well, but it's a much larger part overall. I prefer mine for being lower profile while still doing the same work.

**Lesson learned:** Check the Stealthchanger repo thoroghly before designing your own parts to solve problems. However, don't be afraid to make your own anyway if you have what you feel is a better idea for your setup and needs.

## SLS Shuttle and Backplates

On a conceptual level, I was very interested in using SLS PA12 nylon processing for the shuttle and toolhead backplates. I ordered these from Xometry, whom I've had good experiences with in the past.

Upon outfitting with pins and magnets, the initial fitup was INCREDIBLY good. I adjusted the tilt screws and got them all installed. 

Unfortunately, in practice, I found that one of my backplates was perfectly usable, but the other had a slight deformation on the OptoTAP mounting screw holes. In SLS processing, there is only really one step where this can happen, and that's in the phase immediately after the printing process where the entire printing chamber is allowed to cool to ambient temperature in order to prevent the parts in the cake from warping during removal. My theory is that my problematic backplate was part of a batch which was pulled out of the chamber without being fully allowed to cool, which introduced around 0.25mm of warp. I attempted to fix this by dremelling out the screw hole location and filling with epoxy, but this was messy and didn't provide good results.

However, the SLS shuttle is working great with both the "good" SLS backplate and my previously-made FDM backplates.

It is worth noting that a CNC shuttle option now exists from Fysetc, and soon from LDO as well. The community has been praising these so far, with the caveat that your backplates will likely have to undergo the heat-treating process again in order to fit up perfectly.

**Lesson learned:** If your FDM shuttle and backplates are working well and are printed from high-quality materials, there is no reason to go with SLS replacements. It may be worth it to use a CNC'd aluminum shuttle if you are having durability issues with your shuttle.

## Piano Wire Umbilical Management

From the first moment I installed the 1mm piano wire for umbilical control, I realized they were too stiff to run all the way to the toolhead, as it would pull the toolhead forward when it was near Y max - throwing off QGL and bed mesh results pretty significantly. There is another option to use 0.3mm x 3mm spring steel, but the most readily-available option for this is to purchase via Aliexpress. If you're like me, waiting 2-3 weeks for your parts to arrive means your printer is going to be essentially unusable for 2-3 weeks. 

Using closer to a 0.6mm-0.8mm piano wire so it can be constrained on the toolhead would help with this, 1mm is just seemingly too stiff.

After this didn't work out very well, I decided to try IGUS ChainFlex cabling from West3D. This initially seemed promising, however the cable began to sag slightly after around 25 hours of ABS-printing chamber temperatures. Not a great result for cable that costs about $5/ft.

Finally, some folks in the DSD Discord tried to replicate what Prusa has done for their umbilical management on the XL, where they use nylon strips for stiffening. This was accomplished using fairly large zipties. I replicated this in my own setup using 36" zipties, which are around 9mm wide and 2.5mm thick. These provided fantastic results and are what I recommend everyone use.

**Lesson learned:** Big nylon zipties are beating the pants off of every other umbilical support option so far.

## Combatting Ooze

Every toolhead is going to ooze a little bit. When tools are travelling from the docks to the print, there will usually be at least a few MM of ooze. This boils down to the following factors:
- Retraction
- Filament printing temperature
- Tool change times

First, go through your firmware and slicer settings to find what your retraction settings are. I have found a ton of spots in OrcaSlicer and in Toolchanger where retraction is set to 2mm, and many of them stack. At one point, my extruders were trying to pull back 8mm of filament when a print was paused and then cancelled. Other times, it would retract 4-8mm during tool changes, and when unretracting, the remaining filament in the nozzle would get rapidly shoved out and create an ooze trail.

Second, if you haven't done one in a while, print temperature towers with each filament you want to use and the tools you want to use it on. Pick the temperature that looks the best, has the best bridging, and is cold as possible. Add 5-10C to it if you intent to print at rapid speeds (or possibly more if you use HF nozzles). This should help minimize how much the filament will ooze just from melting in the nozzle as the tool travels.

Third, your tool change times. You should get these as fast as possible without introducing unreliability. Run [Klipper Auto Speed](https://github.com/EasterWorks/Cergs-Stealthchanger/blob/main/Extrapolation/Klipper%20Auto%20Speed/readme.md) to determine your X, Y, and Z max travel sppeds and accelerations.

With these three factors dialed in, your ooze should be reduced significantly.

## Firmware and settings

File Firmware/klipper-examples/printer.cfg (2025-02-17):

[include mainsail.cfg]

[mcu]
##  Obtain definition by "ls /dev/serial/by-id/*" then unplug to verify
##--------------------------------------------------------------------
serial: /dev/serial/by-id/usb-Klipper_stm32f446xx_3D003D000850314D35323820-if00
restart_method: command
##--------------------------------------------------------------------

[include stealthburner_leds.cfg]

[include Stealthchanger/nest.cfg]

[include Stealthchanger/tool_detection.cfg]
[include Stealthchanger/toolchanger.cfg]

[include Stealthchanger/t0.cfg]
[include Stealthchanger/t1.cfg]
[include Stealthchanger/t2.cfg]
[include Stealthchanger/t3.cfg]

[include Stealthchanger/homing.cfg]
[include Stealthchanger/calibrate-offsets.cfg]
[include Stealthchanger/toolchanger-macros.cfg]

[include bigtreetech-hbb.cfg]

[exclude_object]

[printer]
kinematics: corexy
max_velocity: 350 
max_accel: 8000 
max_z_velocity: 150 
max_z_accel: 400
square_corner_velocity: 5.0

[force_move]
enable_force_move: True

[rounded_path]
resolution: 0.2 # the length of a circle approximation segments.
replace_g0: False # Use at your own risk

[input_shaper]

#####################################################################
#   X/Y Stepper Settings
#####################################################################
##  B Stepper - Left
##  Connected to MOTOR0
##  Endstop connected to DIAG0
[stepper_x]
step_pin: PF13
dir_pin: PF12
enable_pin: !PF14
rotation_distance: 40
microsteps: 32
full_steps_per_rotation:400  #set to 200 for 1.8 degree stepper
endstop_pin: PG6
position_min: 0
position_endstop: 300
position_max: 300
homing_speed: 50   #Max 100
homing_retract_dist: 5
homing_positive_dir: true

[tmc2209 stepper_x]
uart_pin: PC4
interpolate: false
run_current: 0.8
sense_resistor: 0.110
stealthchop_threshold: 0

##  A Stepper - Right
##  Connected to MOTOR1
##  Endstop connected to DIAG1
[stepper_y]
step_pin: PG0
dir_pin: PG1
enable_pin: !PF15
rotation_distance: 40
microsteps: 32
full_steps_per_rotation:400  #set to 200 for 1.8 degree stepper
endstop_pin: PG9
position_min: -10
position_endstop: 300
position_max: 300
homing_speed: 50  #Max 100
homing_retract_dist: 5
homing_positive_dir: true

[tmc2209 stepper_y]
uart_pin: PD11
interpolate: false
run_current: 0.8
sense_resistor: 0.110
stealthchop_threshold: 0
 
#####################################################################
#   Z Stepper Settings
#####################################################################

## Z0 Stepper - Front Left from viewer's perspective
##  Connected to MOTOR2_1
##  Endstop connected to DIAG_2
[stepper_z]
step_pin: PF11
dir_pin: PG3
enable_pin: !PG5
rotation_distance: 40
gear_ratio: 80:16
microsteps: 32
endstop_pin: probe:z_virtual_endstop
#position_endstop:
homing_retract_dist: 2 # beacon doesn't use homing retract, setting to anything other than 0 will cause errors.
homing_positive_dir: false
position_max: 300
position_min: -15

[tmc2209 stepper_z]
uart_pin: PC6
interpolate: false
run_current: 0.8
sense_resistor: 0.110
stealthchop_threshold: 0 #999999

##  Z1 Stepper - Rear Left  from viewer's perspective
##  Connected to MOTOR3
[stepper_z1]
step_pin: PG4
dir_pin: !PC1
enable_pin: !PA0
rotation_distance: 40
gear_ratio: 80:16
microsteps: 32

[tmc2209 stepper_z1]
uart_pin: PC7
interpolate: false
run_current: 0.8
sense_resistor: 0.110
stealthchop_threshold: 0 #999999

##  Z2 Stepper - Rear Right from viewer's perspective
##  Connected to MOTOR4
[stepper_z2]
step_pin: PF9
dir_pin: PF10
enable_pin: !PG2
rotation_distance: 40
gear_ratio: 80:16
microsteps: 32

[tmc2209 stepper_z2]
uart_pin: PF2
interpolate: false
run_current: 0.8
sense_resistor: 0.110
stealthchop_threshold: 0 #999999

##  Z3 Stepper - Front Right from viewer's perspective
##  Connected to MOTOR5
[stepper_z3]
step_pin: PC13
dir_pin: !PF0
enable_pin: !PF1
rotation_distance: 40
gear_ratio: 80:16
microsteps: 32

[tmc2209 stepper_z3]
uart_pin: PE4
interpolate: false
run_current: 0.8
sense_resistor: 0.110
stealthchop_threshold: 0 #999999


#####################################################################
#   Bed Heater
#####################################################################

[heater_bed]
##  SSR Pin - HE1
##  Thermistor - TB
heater_pin: PA1
##  Validate the following thermistor type to make sure it is correct
##  Keenovo branded bed heaters should use Generic 3950
##  LDO branded bed heaters will have the sensor type labelled on the heater
##  See https://www.klipper3d.org/Config_Reference.html#common-thermistors for additional options
sensor_type: Generic 3950 
sensor_pin: PF3
##  Adjust Max Power so your heater doesn't warp your bed. Rule of thumb is 0.4 watts / cm^2 .
max_power: 0.6
min_temp: 0
max_temp: 120
control: pid
pid_Kp=40.328 
pid_Ki=1.054 
pid_Kd=385.633


#####################################################################
#   Fan Control
#####################################################################

[controller_fan controller_fan]
##  Controller fan - CNC_FAN2
pin: PD12
kick_start_time: 0.5
heater: heater_bed
fan_speed: 0.5

#####################################################################
#   LED Control
#####################################################################

[output_pin caselight]
## Chamber Lighting - CNC_FAN5
pin: PD15
pwm:true
shutdown_value: 0
value:0
cycle_time: 0.01

#####################################################################
#   Additional Sensors
#####################################################################

[thermistor CMFB103F3950FANT]
temperature1: 0.0
resistance1: 32116.0
temperature2: 40.0
resistance2: 5309.0
temperature3: 80.0
resistance3: 1228.0

#####################################################################
#   Homing and Gantry Adjustment Routines
#####################################################################

[idle_timeout]
timeout: 48000

[bed_mesh]
speed: 600 #360 very safe speed
algorithm: bicubic # default: lagrange
horizontal_move_z: 5
probe_count: 7,7 # default: 3,5 previous: 5,5
zero_reference_position: 150,150
mesh_min: 60, 30
mesh_max: 240,240

[quad_gantry_level]
gantry_corners:
   -60,-10
   360,370
##  Probe points
points:
   50,25
   50,225
   250,225
   250,25

speed: 600
horizontal_move_z: 5
retries: 20
retry_tolerance: 0.0250 #changed from 0.00750 temporarily
max_adjust: 20

#####################################################################
#   Macros
#####################################################################

[gcode_macro M600]
gcode:
    {% set X = params.X|default(50)|float %}
    {% set Y = params.Y|default(0)|float %}
    {% set Z = params.Z|default(10)|float %}
    SAVE_GCODE_STATE NAME=M600_state
    PAUSE
    G91
    G1 E-.8 F2700
    G1 Z{Z}
    G90
    G1 X{X} Y{Y} F3000
    G91
    G1 E-50 F1000
    RESTORE_GCODE_STATE NAME=M600_state

[gcode_macro CLEAN_NOZZLE]
variable_start_x: 245
variable_start_y: 299
variable_start_z: 0
variable_wipe_dist: 33
variable_wipe_qty: 5
variable_wipe_spd: 200
variable_raise_distance: 25
variable_return_y: 290 # tells the printhead to move 10mm closer to the bed after cleaning

gcode:
  STATUS_CLEANING
  {% if "xyz" not in printer.toolhead.homed_axes %}
    G28
  {% endif %}
 
  G90                                            ; absolute positioning
  ## Move nozzle to start position
  G1 X{start_x} Y{start_y} F6000
  G1 Z{start_z} F1500

  ## Wipe nozzle
  {% for wipes in range(1, (wipe_qty + 1)) %}
    G1 X{start_x + wipe_dist} F{wipe_spd * 60}
    G1 X{start_x} F{wipe_spd * 60}
  {% endfor %}

  ## Raise nozzle
  G1 Z{raise_distance}
  G1 Y{return_y} F1500
  STATUS_READY


[gcode_macro G32]
gcode:
    STATUS_HOMING
    G28
    STATUS_CALIBRATING_Z
    QUAD_GANTRY_LEVEL
    G28
    G0 X150 Y150 Z30 F4000
    STATUS_READY
    
   
[gcode_macro PRINT_START]
gcode:
    STATUS_HOMING
    G28    #pre-print homing
    CLEAN_NOZZLE #scrub the nozzle
    BED_MESH_CALIBRATE #mesh the bed
    G28 #home again after meshing
    G1 Z20 F3000                   ; move nozzle away from bed
    STATUS_PRINTING                ; change Stealthburner light status to STATUS_PRINTING
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

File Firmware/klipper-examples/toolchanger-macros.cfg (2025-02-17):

# Original written by Viesturs Zarins
# Modified by Justin F. Hallett

[gcode_macro _TOOLCHANGER_VARS]
variable_fan_speed: 0
gcode:


[gcode_macro _TOOLCHANGER_DISABLE_EXTRUDER_STEPPERS]
description: Disable all extruder steppers
gcode:
  {% for toolname in printer.toolchanger.tool_names %}
    SET_STEPPER_ENABLE STEPPER={printer[toolname].extruder} ENABLE=0
  {% endfor %}


[gcode_macro _MOVE_TO_CENTER]
gcode:
  {% set max_y = printer.configfile.config["stepper_y"]["position_max"]|float %}
  {% set max_x = printer.configfile.config["stepper_x"]["position_max"]|float %}
  {% if "xyz" not in printer.toolhead.homed_axes %}
    G28
  {% endif %}
  G90 ; absolute mode
  G0 X{max_x//2} Y{max_y//2} F12000


[gcode_macro _TAP_PROBE_ACTIVATE]
description: Ensure safe temp for bed probing
gcode:
  {% set max_temp = params.TEMP|default(150)|int %}
  {% set actual_temp = printer[params.HEATER].temperature %}
  {% set target_temp = printer[params.HEATER].target %}
  {% if target_temp > max_temp %}
    { action_respond_info('Extruder temperature target of %.1fC is too high, lowering to %.1fC' % (target_temp, max_temp)) }
    SET_HEATER_TEMPERATURE HEATER={params.HEATER} TARGET={ max_temp }
  {% endif %}
  # Temperature target is already low enough, but nozzle may still be too hot.
  {% if actual_temp > max_temp + 2 %}
    { action_respond_info('Extruder temperature %.1fC is still too high, waiting until below %.1fC' % (actual_temp, max_temp)) }
    TEMPERATURE_WAIT SENSOR={params.HEATER} MAXIMUM={ max_temp }
  {% endif %}


[gcode_macro M104]
rename_existing: M104.1
description: [T<index>] [S<temperature>]
  Set tool temperature.
  T= Tool number, optional. If this parameter is not provided, the current tool is used.
  S= Target temperature
gcode:
  STATUS_HEATING
  {% if params.T is defined %}
    {% set newparameters = "" %}
    {% set newparameters = newparameters ~ " T="~params.T %}
    {% if params.S is defined %}
      {% set newparameters = newparameters ~ " TARGET="~params.S %}
    {% endif %}
    SET_TOOL_TEMPERATURE{newparameters}
  {% else %}
    M104.1 {rawparams}
  {% endif %}


[gcode_macro M109]
rename_existing: M109.1
description: [T<index>] [S<temperature>]
  Set tool temperature and wait.
  T= Tool number, optional. If this parameter is not provided, the current tool is used.
  S= Target temperature
gcode:
  STATUS_HEATING
  {% if params.T is defined %}
    {% set newparameters = "" %}
    {% set newparameters = newparameters ~ " T="~params.T %}
    {% if params.S is defined %}
      {% set newparameters = newparameters ~ " TARGET="~params.S %}
    {% endif %}
    SET_TOOL_TEMPERATURE WAIT=1 {newparameters}
  {% else %}
    M109.1 {rawparams}
  {% endif %}


[gcode_macro _TOOL_BEFORE_CHANGE]
gcode:
  STATUS_BUSY
  {% set tn = params.TN|string %}
  {% set tool = printer['tool ' + tn] %}
  {% if printer["gcode_macro T" + tool.tool_number|string ] %}
    SET_GCODE_VARIABLE MACRO=T{tool.tool_number} VARIABLE=color VALUE="''"
  {% endif %}  


[gcode_macro _TOOL_AFTER_CHANGE]
gcode:
  {% set tn = params.TN|string %}
  {% set tool = printer['tool ' + tn] %}
  {% set max_z = printer.configfile.config["stepper_z"]["position_max"]|float %}
  {% if printer["gcode_macro T" + tool.tool_number|string ] %}
    SET_GCODE_VARIABLE MACRO=T{tool.tool_number} VARIABLE=color VALUE="'c44'"
  {% endif %}
  {% if 'input_shaper' in printer.configfile.config %}
    {% set default_x_freq = printer.configfile.config['input_shaper']['shaper_freq_x']|default(0)|float %}
    {% set default_x_type = printer.configfile.config['input_shaper']['shaper_type_x']|default('mzv')|string %}
    {% set default_x_damping = printer.configfile.config['input_shaper']['damping_ratio_x']|default(0.1)|float %}
    {% set default_y_freq = printer.configfile.config['input_shaper']['shaper_freq_y']|default(0)|float %}
    {% set default_y_type = printer.configfile.config['input_shaper']['shaper_type_y']|default('mzv')|string %}
    {% set default_y_damping = printer.configfile.config['input_shaper']['damping_ratio_y']|default(0.1)|float %}
    SET_INPUT_SHAPER SHAPER_TYPE_X={tool.params_input_shaper_type_x if tool.params_input_shaper_type_x else default_x_type} SHAPER_FREQ_X={tool.params_input_shaper_freq_x if tool.params_input_shaper_freq_x else default_x_freq} SHAPER_TYPE_Y={tool.params_input_shaper_type_y if tool.params_input_shaper_type_y else default_y_type} SHAPER_FREQ_Y={tool.params_input_shaper_freq_y if tool.params_input_shaper_freq_y else default_y_freq} DAMPING_RATIO_X={tool.params_input_shaper_damping_ratio_x if tool.params_input_shaper_damping_ratio_x else default_x_damping} DAMPING_RATIO_Y={tool.params_input_shaper_damping_ratio_y if tool.params_input_shaper_damping_ratio_y else default_y_damping}
    STATUS_PRINTING
  {% endif %}
  

[gcode_macro _TOOL_DROPOFF]
gcode:
  STATUS_BUSY
  {% set tn = params.TN|string %}
  {% set tool = printer['tool ' + tn] %}
  {% set x = tool.params_park_x|float %} 
  {% set y = tool.params_park_y|float %} 
  {% set z = tool.params_park_z|float %}
  {% set safe_y = tool.params_safe_y|float %}
  {% set fast = tool.params_fast_speed|float %}
  {% set path = tool['params_dock_' + tool.params_dock_type + '_path'] + [{'f':0.5}] + tool['params_changer_' + tool.params_changer_type + '_path'] %}
  {% set max_z = printer.configfile.config["stepper_z"]["position_max"]|float %}
  {% set cur_z = printer.toolhead.position[2]|float %}
  G90
  ; Move 1 mm up to avoid crashing into things
  G0 Z{ [cur_z+1.0, max_z]|min } F{fast}    
  #   ##############  Move up to the dock  ##############    
  ROUNDED_G0 Y={safe_y} D=20 F={fast}
  ROUNDED_G0 X={x} D=150 F={fast}
  ROUNDED_G0 Z={z + path[0].get('z', 0)|float} D=20 F={fast}
  ROUNDED_G0 Y={y + path[0].get('y', 0)|float} X={x + path[0].get('x', 0)|float} D=0 F={fast}
  STOP_TOOL_PROBE_CRASH_DETECTION
  #  ############## Run the path ##############
  {% for pos in path %}
    G0 Y{y + pos.get('y', 0)|float} X{x + pos.get('x', 0)|float} Z{z + pos.get('z', 0)|float} F{tool.params_path_speed|float * (pos.get('f', 1.0)|float) }
  {% endfor %}
  SET_GCODE_VARIABLE MACRO=_TOOLCHANGER_VARS VARIABLE=fan_speed VALUE={ printer[tool.fan].speed * 255|default(0)|int }
  M106 S0 T{tn}


[gcode_macro _TOOL_PICKUP]
gcode:  
  {% set tn = params.TN|string %}
  {% set tool = printer['tool ' + tn] %}
  {% set x = tool.params_park_x|float %} 
  {% set y = tool.params_park_y|float %} 
  {% set z = tool.params_park_z|float %}
  {% set close_y = tool.params_close_y|float %}
  {% set fast = tool.params_fast_speed|float %}
  {% set path = tool['params_dock_' + tool.params_dock_type + '_path'] + [{'f':0.5}] + tool['params_changer_' + tool.params_changer_type + '_path'] %}
  G90
  #   ##############  Fast to the last point  ##############
  ROUNDED_G0 Y={close_y} F={fast} D=5
  ROUNDED_G0 X={x} Z={z + path[-1].get('z', 0)|float} F={fast} D=5
  ROUNDED_G0 Y={y + path[-1].get('y', 0)|float} X={x + path[-1].get('x', 0)|float} F={fast} D=0
  # Wait for temp before actually picking up the tool, while the nozzle is resting on it's pad.
    
  {% if tool.extruder %}
    M109 T{tool.tool_number} S{printer[tool.extruder].target|int}
  {% endif %}
  # Run the path in reverse
  {% for pos in path|reverse %}
    G0 Y{y + pos.get('y', 0)|float} X{x + pos.get('x', 0)|float} Z{z + pos.get('z', 0)|float} F{tool.params_path_speed|float * (pos.get('f', 1.0)|float) }      
    {% if 'f' in pos %} # Use the f presence as marker that we have made contact with the tool.
      START_TOOL_PROBE_CRASH_DETECTION T={tool.tool_number}
    {% endif %}
  {% endfor %}
  SET_STEPPER_ENABLE STEPPER={tool.extruder} ENABLE=1
  # Restore the position with smooth rounded move.
  ROUNDED_G0 Y={tool.params_safe_y} F={fast} D=20
  {% if 'Z' in restore_position %}
    ROUNDED_G0 Z={restore_position.Z} F={fast} D=150
  {% endif %}
  {% if 'X' in restore_position %}
    ROUNDED_G0 X={restore_position.X} F={fast} D=1000
  {% endif %}
  {% if 'Y' in restore_position %}
    ROUNDED_G0 Y={restore_position.Y} F={fast} D=0
  {% endif %}
  ROUNDED_G0 D=0
  M106 S{printer["gcode_macro _TOOLCHANGER_VARS"].fan_speed} T{tn}
  STATUS_PRINTING


[gcode_macro _INITIALIZE_FROM_DETECTED_TOOL]
gcode:
  {% if printer.tool_probe_endstop.active_tool_number|int == -1 %} 
    {% if (printer.toolchanger.homing_toolless and 'z' in printer.toolhead.homed_axes) %}
      RESPOND TYPE=echo MSG='No tool found, picking up T{printer.toolchanger.tool_numbers[0]}'
      SELECT_TOOL T={printer.toolchanger.tool_numbers[0]} FORCE_PICKUP=1 RESTORE_AXIS=Z
      DETECT_ACTIVE_TOOL_PROBE
      INITIALIZE_TOOLCHANGER T={printer.toolchanger.tool_numbers[0]}
    {% else %}
      RESPOND TYPE=error MSG='Failed to detect active tool'
      PAUSE
    {% endif %}
  {% else %}
    INITIALIZE_TOOLCHANGER T={printer.tool_probe_endstop.active_tool_number}
  {% endif %}    
  STATUS_READY
 

[gcode_macro TOOL_ALIGN_START]
gcode:    
  INITIALIZE_TOOLCHANGER # Detect current tool
  _TOOL_ALIGN_START
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

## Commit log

2024-12-11 Create STL-Readme
2024-12-11 added x-axis-prod and mgn12 shuttle v1's
    [MGN12 Shuttle.stl, x-axis-prod.stl]
2024-12-11 Update STL-Readme
    text wrapping
2024-12-13 Create printer.cfg
    Initial printer.cfg upload - my full configuration from my Voron 2.4r2.
    [printer.cfg]
2024-12-13 Create toolchanger.cfg
    Initial addition of my toolchanger.cfg file. Mostly stock.
    [toolchanger.cfg]
2024-12-13 Create toolchanger-macros.cfg
    Initial addition of toolchanger-macros.cfg - this is straight from DraftShift's toolchanger repo, the only change was adding "TOOLCHANGER_" to the beginning of PRINT_START and PRINT_END for debugging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
    [toolchanger-macros.cfg]
2024-12-13 Create tool_detection.cfg
    Initial addition of my tool_detection.cfg. Entirely stock, from DraftShift's toolchanger repo.
    [tool_detection.cfg]
2024-12-13 Create stealthchanger_macros.cfg
    Initial commit. NOTE: Some of these macros are duplicated, like PRINT_START_TOOLCHANGER. Will clean this up and commit a final version later
    [stealthchanger_macros.cfg]
2024-12-13 Create homing.cfg
    initial homing.cfg commit, one modification on lines 27-28
    [homing.cfg]
2024-12-13 Create calibrate-offsets.cfg
    Initial commit of calibrate-offsets.cfg. This is stock from V's Tapchanger repo with the exception of commenting out [tools_calibrate] in its entirety, because I have no idea what PF5 is supposed to 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
    [calibrate-offsets.cfg]
2024-12-13 Create t0.cfg
    added my t0 cfg
    [t0.cfg]
2024-12-13 Create t1.cfg
    added t1 cfg
    [t1.cfg]
2024-12-24 Update t0.cfg
    updated with fixed ADXL1345 blocks and docking position for T0
    [t0.cfg]
2024-12-24 Update t1.cfg
    un-inverted probe pin, which was done initially for testing
    [t1.cfg]
2024-12-24 Update printer.cfg
    fixed bad start_gcode and added TOOLCHANGER_FORCE for future implementation in spamming initialize commands to get around bug where toolhead is detected but not set active, further investigation needed but might be a problem in the original config
    [printer.cfg]
2024-12-30 Update firmware-readme
    added info on calibrating nozzle offset
2024-12-30 Update Hardware-And-Calibration.md
    wip save
2024-12-30 Update Hardware-And-Calibration.md
    formatting
2024-12-30 Update Hardware-And-Calibration.md
    formatting, added next section
2024-12-31 Update Hardware-And-Calibration.md
    more info added, still wip
2024-12-31 Update Hardware-And-Calibration.md
    finalized doc (for now)
2024-12-31 Update Hardware-And-Calibration.md
    added section 0 and updated info in section 8
2024-12-31 Update Hardware-And-Calibration.md
    formatting, removed numbering for easier future edits
2024-12-31 Update Hardware-And-Calibration.md
    cleanup
2025-01-04 Update Hardware-And-Calibration.md
    adding images
2025-01-05 Add files via upload
    added zero-clearance PLA supports
    [zero-clear_supports.stl]
2025-01-05 Update and rename STL-Readme to STL-Readme.md
    formatting, added zero_clearance_support.stl info
2025-01-05 Add files via upload
    replaced old shuttle with fixed one in correct orientation
    [shuttle_redesign.stl]
2025-01-05 Add files via upload
    replaced updated parts
    [shuttle-redesign.stl, x-axis-prod.stl]
2025-01-05 Add files via upload
    redesigned x pod mounting hole geometry to better reflect the Voron standard
    [shuttle-redesign.stl]
2025-01-05 Add files via upload
    fixed messed up geometry on one of the bushing ears
    [shuttle-redesign.stl]
2025-01-05 Update printer.cfg
    added comments
    [printer.cfg]
2025-02-17 Update printer.cfg
    updated
    [printer.cfg]
2025-11-25 Add files via upload
    STL files provided by nicksnoopy on Discord
    [Rapido_v2_Front.stl, Rapido_v2_Rear.stl]
